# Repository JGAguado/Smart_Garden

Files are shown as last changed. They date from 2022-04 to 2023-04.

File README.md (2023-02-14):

[][documentation]
[][releases]
[](LICENSE)
[][tindie]

[][maintenance]
[][buymecoffee]

# Smart Garden
The Smart Garden is an electronic board based on the ESP32 capable of controlling a combination of 4 irrigation valves and/or water pumps, 
supporting AC & DC voltages

<p float="left">
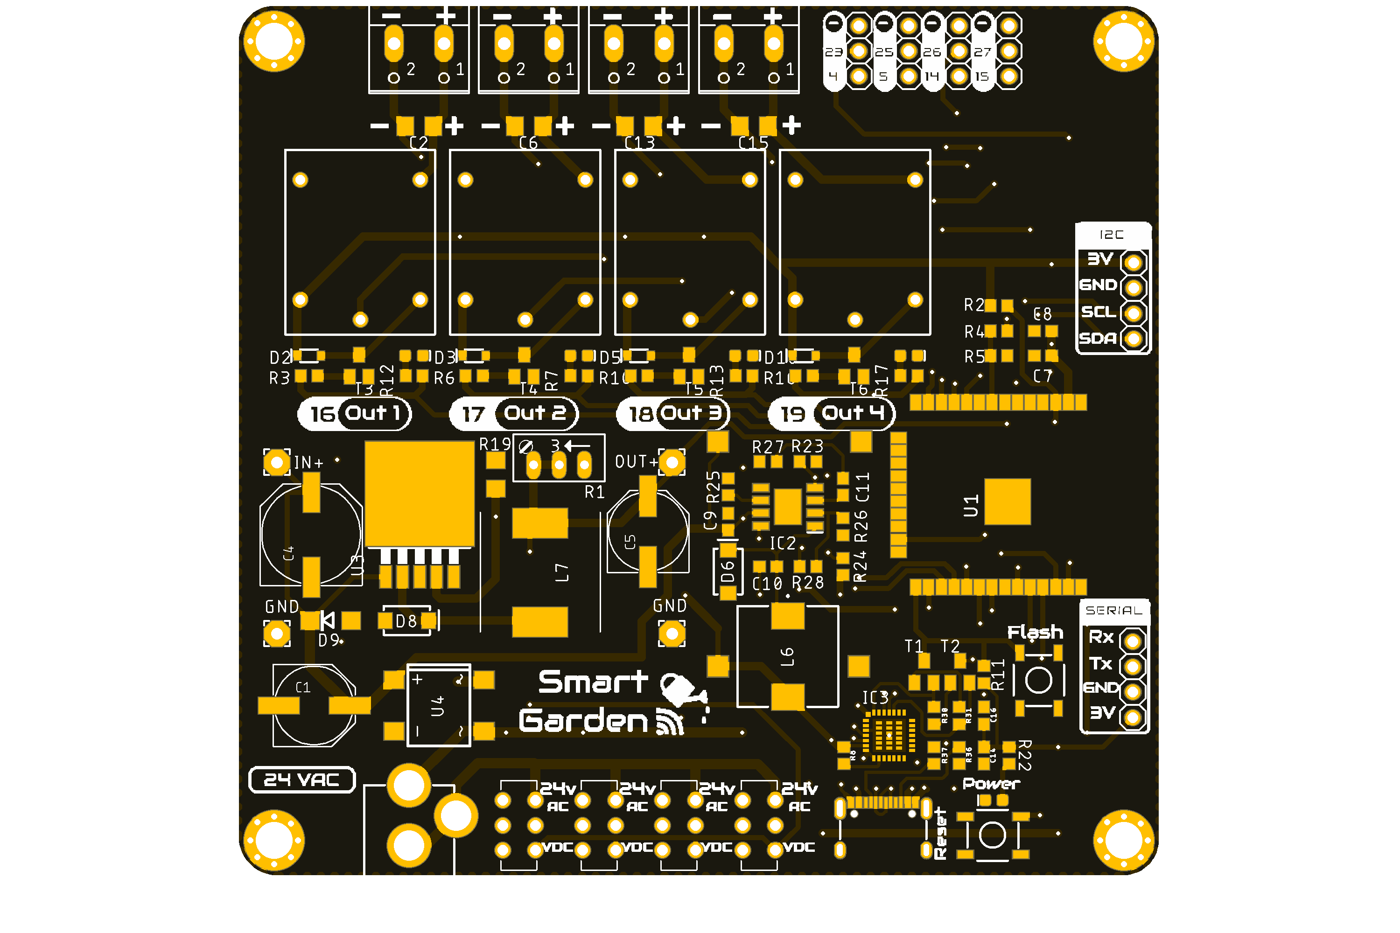
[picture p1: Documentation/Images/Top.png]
   
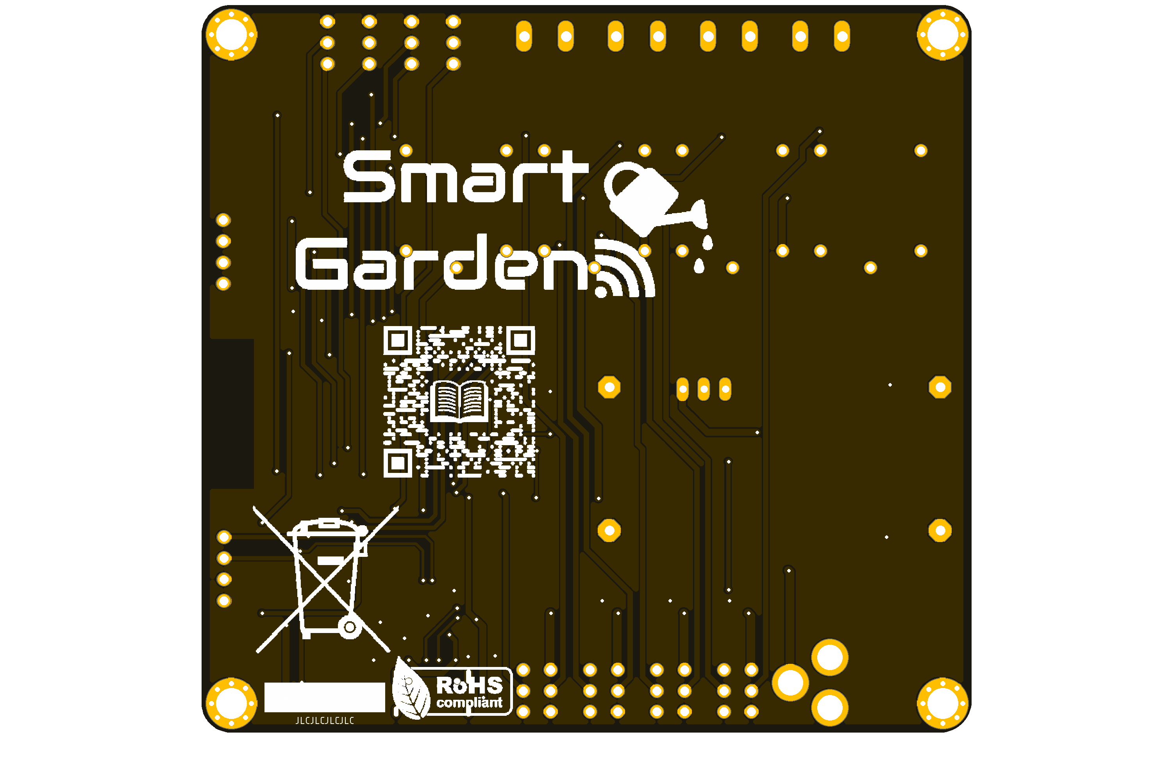
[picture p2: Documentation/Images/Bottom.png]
      
</p>

## Project tree
---
<li><a href="./Design/">Design</a></li>
<li><a href="./Documentation/">Documentation</a></li>

<li><a href="./README.md">README.md</a></li>

[documentation-shield]: https://readthedocs.org/projects/smart-garden/badge/?version=latest&style=for-the-badge
[documentation]: https://smart-garden.readthedocs.io/en/latest/

[releases-shield]: https://img.shields.io/github/release/JGAguado/Smart_Garden.svg?style=for-the-badge
[releases]: https://github.com/JGAguado/Smart_Garden/releases

[license-shield]: https://img.shields.io/badge/License-CC%20BY--NC--SA%204.0-lightgrey.svg?style=for-the-badge

[maintenance-shield]: https://img.shields.io/badge/maintainer-J.%20G.%20Aguado-blue.svg?style=for-the-badge
[maintenance]: https://github.com/JGAguado

[buymecoffee-shield]: https://img.shields.io/badge/buy%20me%20a%20coffee-support-yellow.svg?style=for-the-badge
[buymecoffee]: https://www.buymeacoffee.com/J.G.Aguado

[buyit-shield]: https://img.shields.io/badge/get%20it%20on-tindie-247d84.svg?style=for-the-badge
[tindie]: https://www.tindie.com/products/jgaguado/smart-garden/

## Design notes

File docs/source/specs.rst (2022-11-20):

Technical Specifications
========================

Electrical
----------

.. list-table:: 
    :widths: 50 20 20 20 20
    :header-rows: 1
    :stub-columns: 1

    * - Parameter
      - Symbol
      - Min.
      - Max.
      - Unit
    * - Supply voltage (AC)
      - :math:`V_{AC}`
      - 12
      - 24
      - *V*
    * - Supply voltage (DC)
      - :math:`V_{DC}`
      - 12 
      - 24
      - *V*
    * - Power
      - *P*
      -  
      - 15
      - *W*

Environment
-----------

.. list-table:: 
    :widths: 50 20 20 20 20 20
    :header-rows: 1
    :stub-columns: 1

    * - Parameter
      - Symbol
      - Min.
      - Typ.
      - Max.
      - Unit
    * - Working temperature [1]_
      - :math:`T_{amb}`
      - 0
      - 25 
      - 60
      - *°C*
    * - Storage temperature [1]_
      - :math:`T_{amb}`
      - 0
      - 25 
      - 60
      - *°C*

.. [1] Based on components datasheets.

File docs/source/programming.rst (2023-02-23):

Programming
===========

There are many firmwares supported with the |Product| (almost any supporting the ESP-32). Some of the tested working are: 
 * ESPHome
 * Tasmota
 * Arduino

In any case scenario, and regardless you are using the USB port or the Serial port for programming it, you
will first need to enter the board into flashing mode. For that, press and hold the *Flash* pushbutton
while you reset the board (pressing once the *Reset* pushbutton).

.. Caution::
    When flashing the board, make sure its only powered by the USB/Serial port.

.. Note::
    It is possible that after flashing your board and while rebooting, the ESP-32 has some issues to boot. This is due to a higher 
    demmand of power while

ESPHome
---------
`ESPHome <https://esphome.io>`_ is a well known platform for programming ESP-based devices 
with a very little effort. It is configured via YAML files and supports a wide range of functionalities
and sensors.

.. Important::
    For using ESPHome, and all its funcionalities, you need to have a `Home Assistant <https://www.home-assistant.io>`_ instance running
    in the same network as your |Product|.

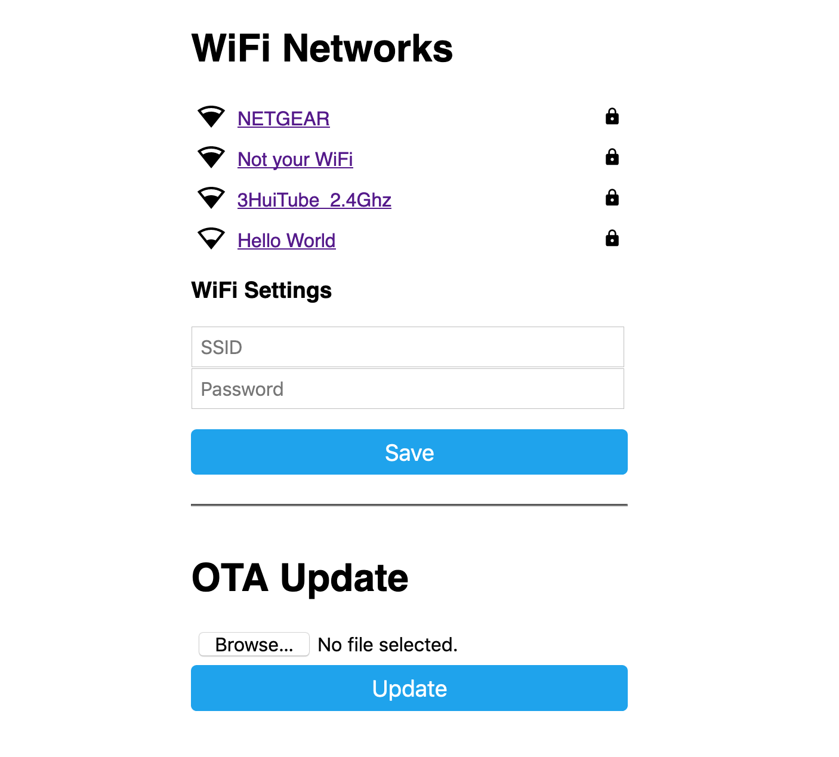
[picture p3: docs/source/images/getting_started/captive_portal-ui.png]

    
The |Product| already comes with an embeded version of ESPHome, that would only require an :term:`OTA` update
to get it ready to work in your network:

1. Power the board, and let it run for 1-2 minutes. When the board cannot connect to a WiFi network, it will 
   create a fallback hotspot.
2. Use a smartphone or tablet and go to the WiFi settings, connect to the recently created *Smart-Garden* hotspot with the password *smartgarden*.
3. Access to the captive portal and open the browser if doesn't pop up automatically.
4. Enter your network setttings and press *Save*.

Now, your ESPHome device is ready to be found by Home Assistant in your network. Add it from the ESPHome section to add 
and edit a customized configuration file.

As an example of such configuration file (and the one flashed on the factory settings of the |Product|) 
with all the :term:`I/O`:

.. literalinclude:: files/configuration.yaml
   :language: yaml
   :linenos:

Tasmota
--------
As an alternative easy-to-use and still powerfull, you can flash Tasmota into the |Product| directly. This option is higly recommendable if you want to want to have an 
Alexa compatible device (based on a Hue emulated bridge) without the need of a full Home Assistant setup.

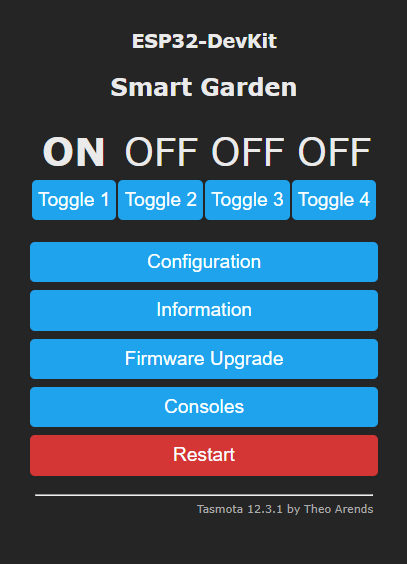
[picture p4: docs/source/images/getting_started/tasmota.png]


The easiest process of flashing Tasmota into your |Product| goes as follows:

1. Plug the |Product| into your computer's USB.
2. Go to the `Tasmota Web Installer <https://tasmota.github.io/install/>`_
3. Follow the process selecting ESP32 as device and select the correct port (remember to enter the board into flashing mode).
4. After the process is completed, press the reset button. 
5. Once rebooted, the |Product| will create a wifi hotspot containing the name *Tasmota*. Connect and enter your WLAN setup on the captive portal. 
6. Get the IP assigned to the board (check your router's connected devices) and enter it into your browser for accessing to the Tasmota's WebUI. 

Now you can customize your board as you want. Let's first assign the output class '*Relay*' to the corresponding outputs 16, 17, 18 and 19. 

In addition, some of these other commands can be entered through the **Console** (*Consoles -> Console*):

 * **Timed output**: With the command ``PulseTime3 300`` you can make that the output 3 turns off after 5 minutes (300s). This option is highly indicated as a safety feature to prevent your home to get floaded.

 * **Interlocks**: With the command ``interlock on`` you can make that ONLY one of the 4 outputs can become active at the same time. For selecting the group of the for relays just use the command ``interlock 1,2,3,4``. This mode can become usefull when your home's water pressure is not high enough for holding more than one watering zone at the same time.

In any case, you can find these and much more commands to customize your Tamota's flashed |Product| on the `official Tasmota documentation <https://tasmota.github.io/docs/Commands/>`_

.. admonition:: And, by the way...
    
    If you want Alexa to directly recognize your |Product| to directly controle each output through voice controls, go to *COnfiguration -> 
    Configure Other* and select the option 'Hue Bridge multi device' emulation.
    
Arduino
--------
If you are still interested in programming directly with the Arduino IDE, the procedure is no 
different than with any other ESP32 devices:

1. Open the Arduino IDE and go to File -> Preferences option.
2. Add to the *Additional Boards Manager URSLs* the url:

.. parsed-literal::

    https://raw.githubusercontent.com/espressif/arduino-esp32/gh-pages/package_esp32_index.json

3. Close the preferences and open in the menu Tools -> Board -> Boards Manager
4. Search for *esp32* and install it. This might take some time
5. Now you can select the board *ESP32 Dev Module* as the target board. Leave the rest of parameters 
   by default.
6. Select the correct port and remember to enter the board into flashing mode before uploading the sketch.

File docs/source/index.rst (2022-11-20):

Smart Garden
###############

.. sidebar:: |Product|

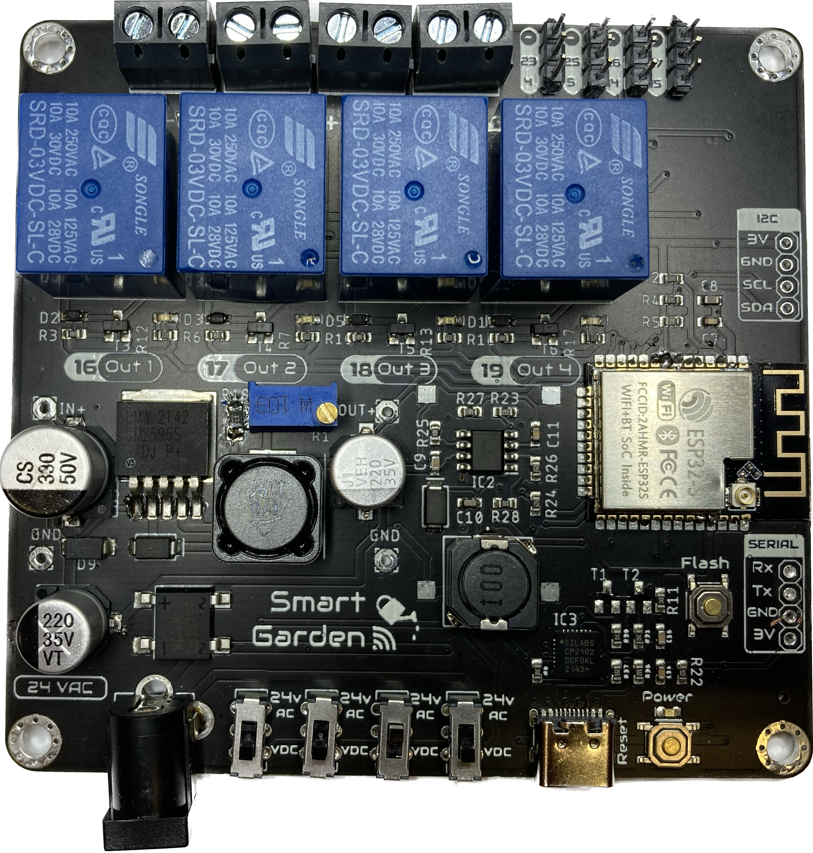
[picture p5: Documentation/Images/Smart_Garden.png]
    

Welcome to the documentation page of the |Product|, an electronic board based on the ESP32 capable of controlling a combination of 4 irrigation valves and/or water pumps, 
supporting AC & DC voltages.

Contents
--------

:doc:`safety`
    How to operate and manipulate the |Product|.

:doc:`getting_started`
    First steps for configuring and working with the |Product|.

:doc:`design`
    Design files of the |Product|.

.. _support:

Technical support
-----------------

If you have technical problems or cannot find the information that you need in the provided documentation, 
please contact me directly:

:Author: |Author|
:Contact: |Email|

:Board: |Product|
:Revision: |Release|
:Date: |Date|

.. toctree::
   :caption: Safety Guidelines
   :maxdepth: 2
   :hidden:

   safety
   
.. toctree::
   :caption: First steps
   :maxdepth: 2
   :hidden:

   getting_started
   programming
   faq

.. toctree::  
   :caption: Design
   :maxdepth: 2
   :hidden:
   
   design   
   specs

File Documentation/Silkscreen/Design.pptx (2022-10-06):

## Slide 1

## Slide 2

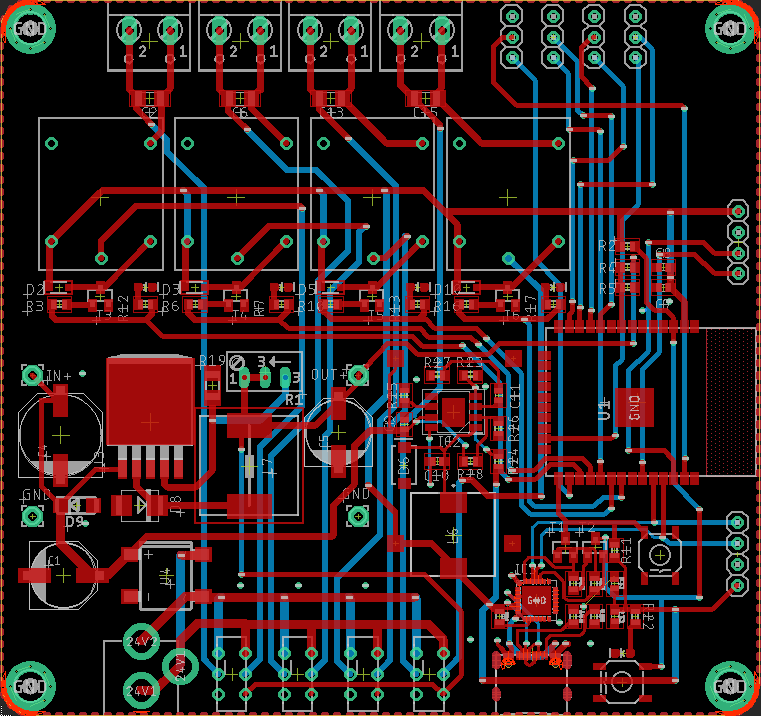
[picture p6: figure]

Out 1

16

Out 2

17

Out 3

18

Out 4

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
Flash

SERIAL

3V

GND

Tx

Rx

Smart Garden

24VAC

24VAC

24VAC

24VAC

24 VAC

Power

VDC

VDC

VDC

VDC

Reset

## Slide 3

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
Out 1

16

Out 2

17

Out 3

18

Out 4

19

Flash

SERIAL

3V

GND

Tx

Rx

Smart Garden

24VAC

24VAC

24VAC

24VAC

24 VAC

Power

VDC

VDC

VDC

VDC

Reset

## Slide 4

Smart Garden

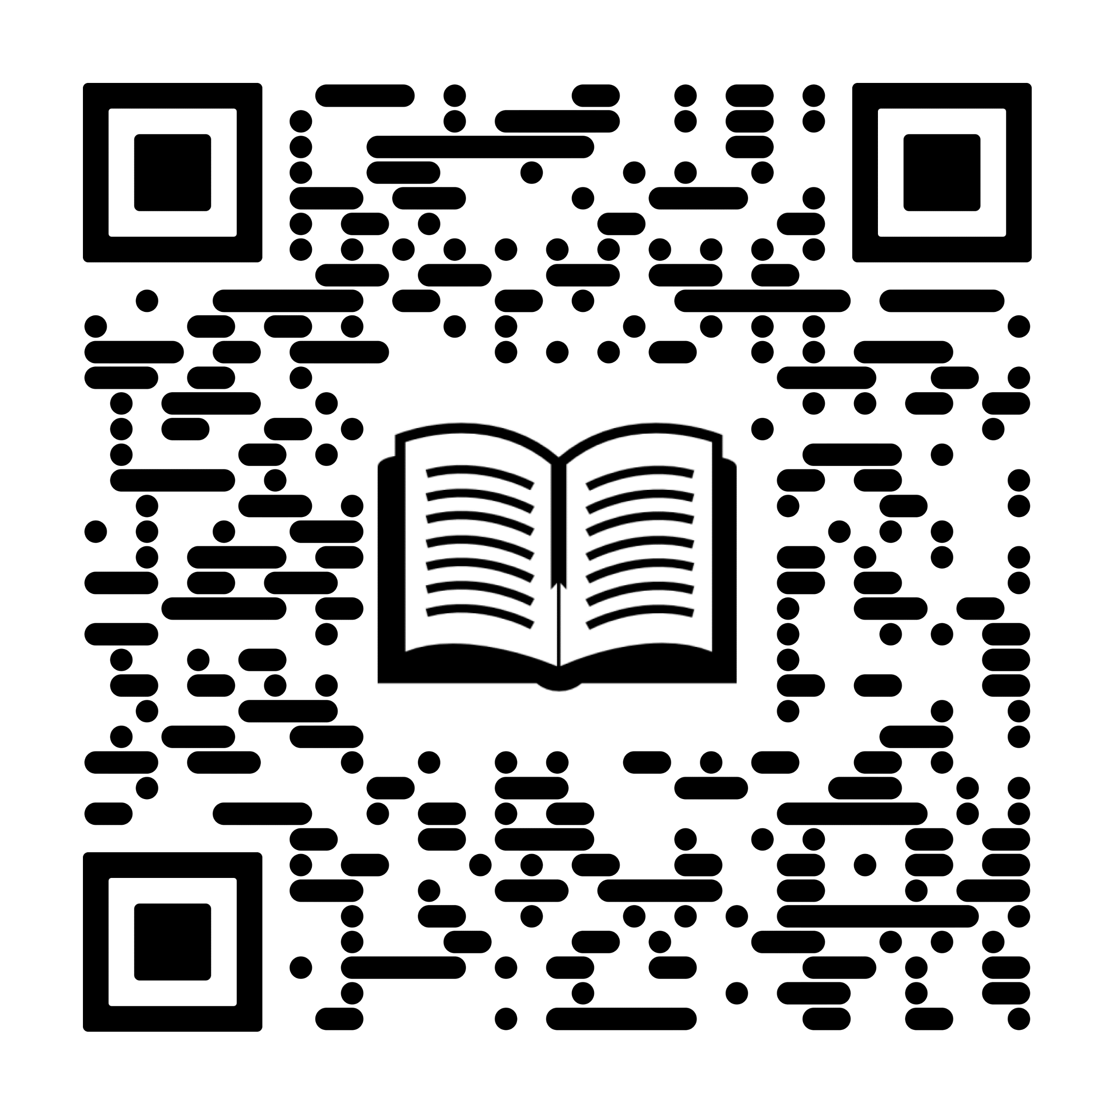
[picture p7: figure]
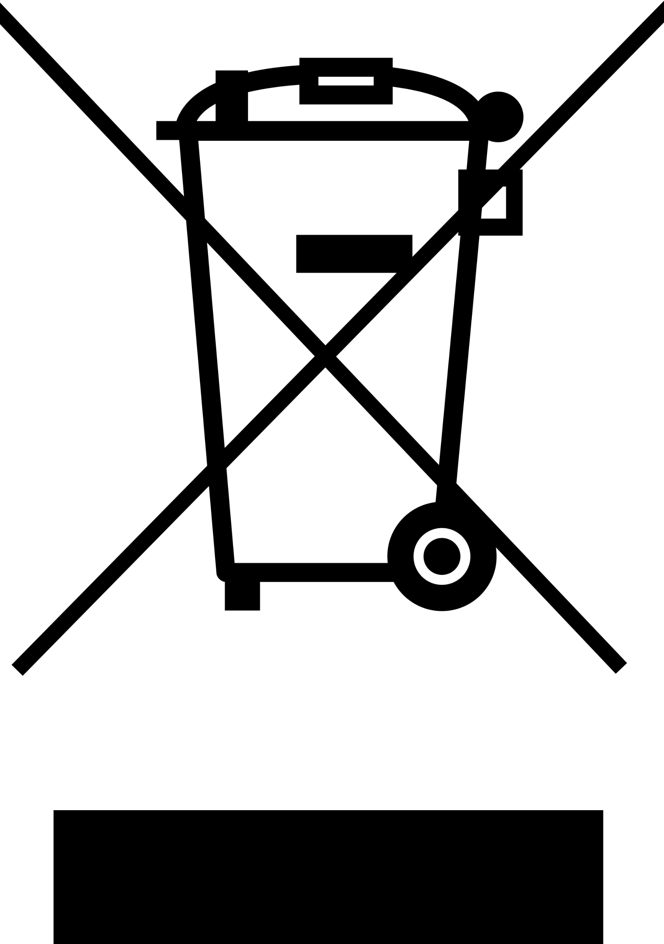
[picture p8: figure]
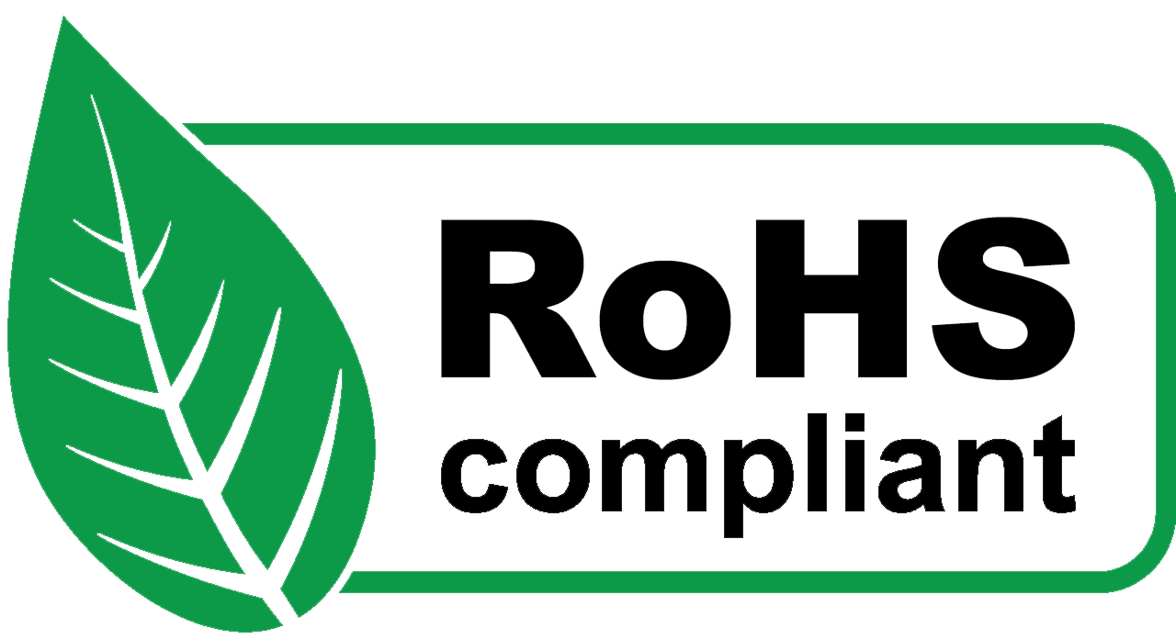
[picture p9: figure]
Umweltrichtlinien

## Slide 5

Smart Garden

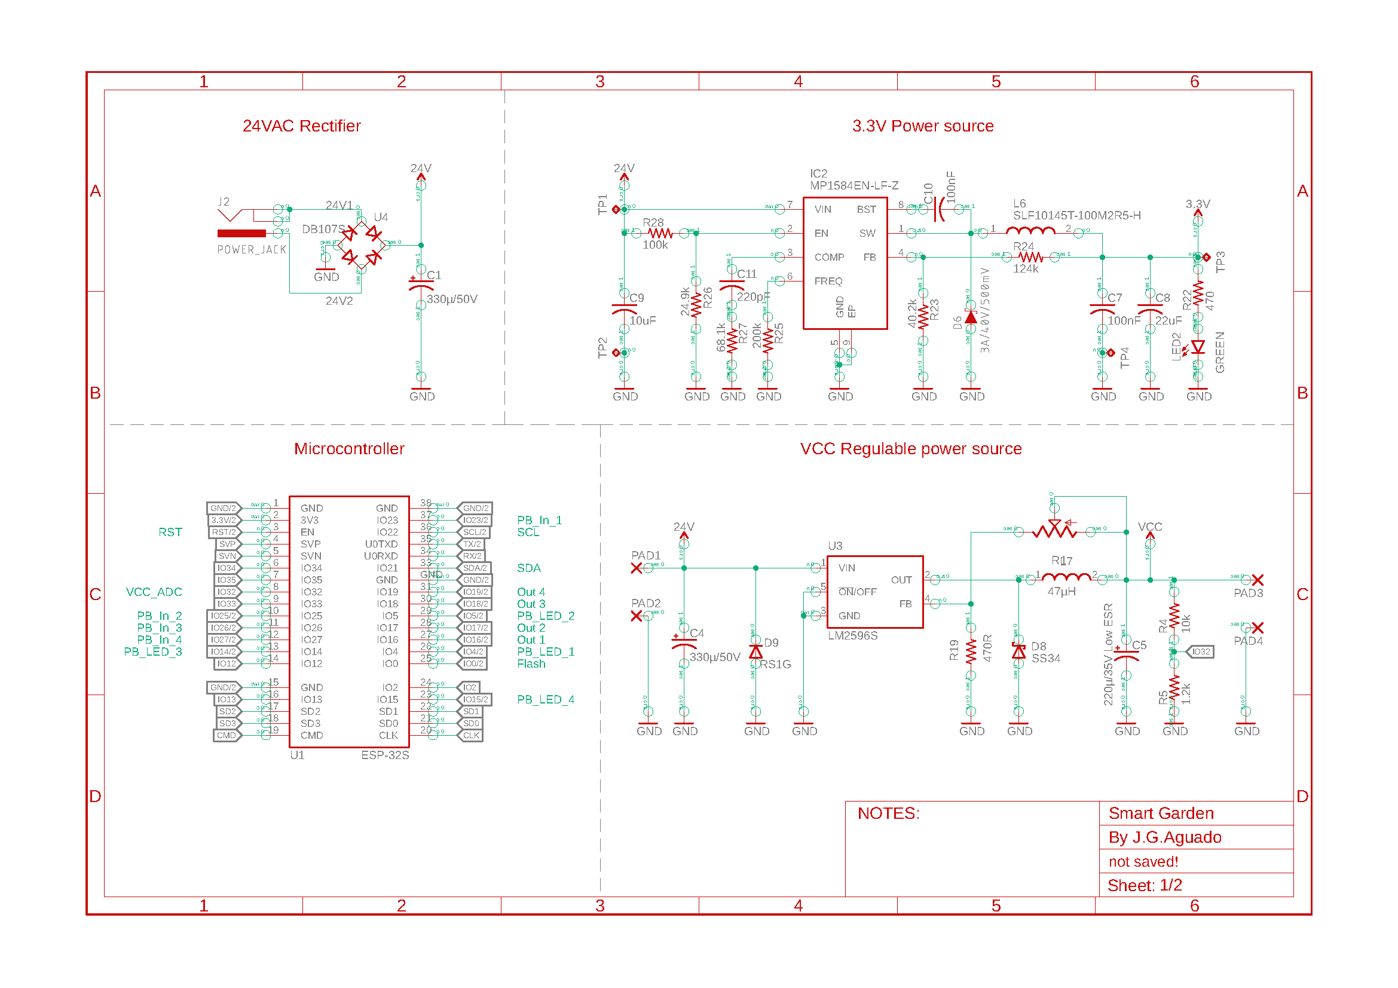
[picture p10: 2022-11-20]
Documentation/Schematics/Schematic_1.png

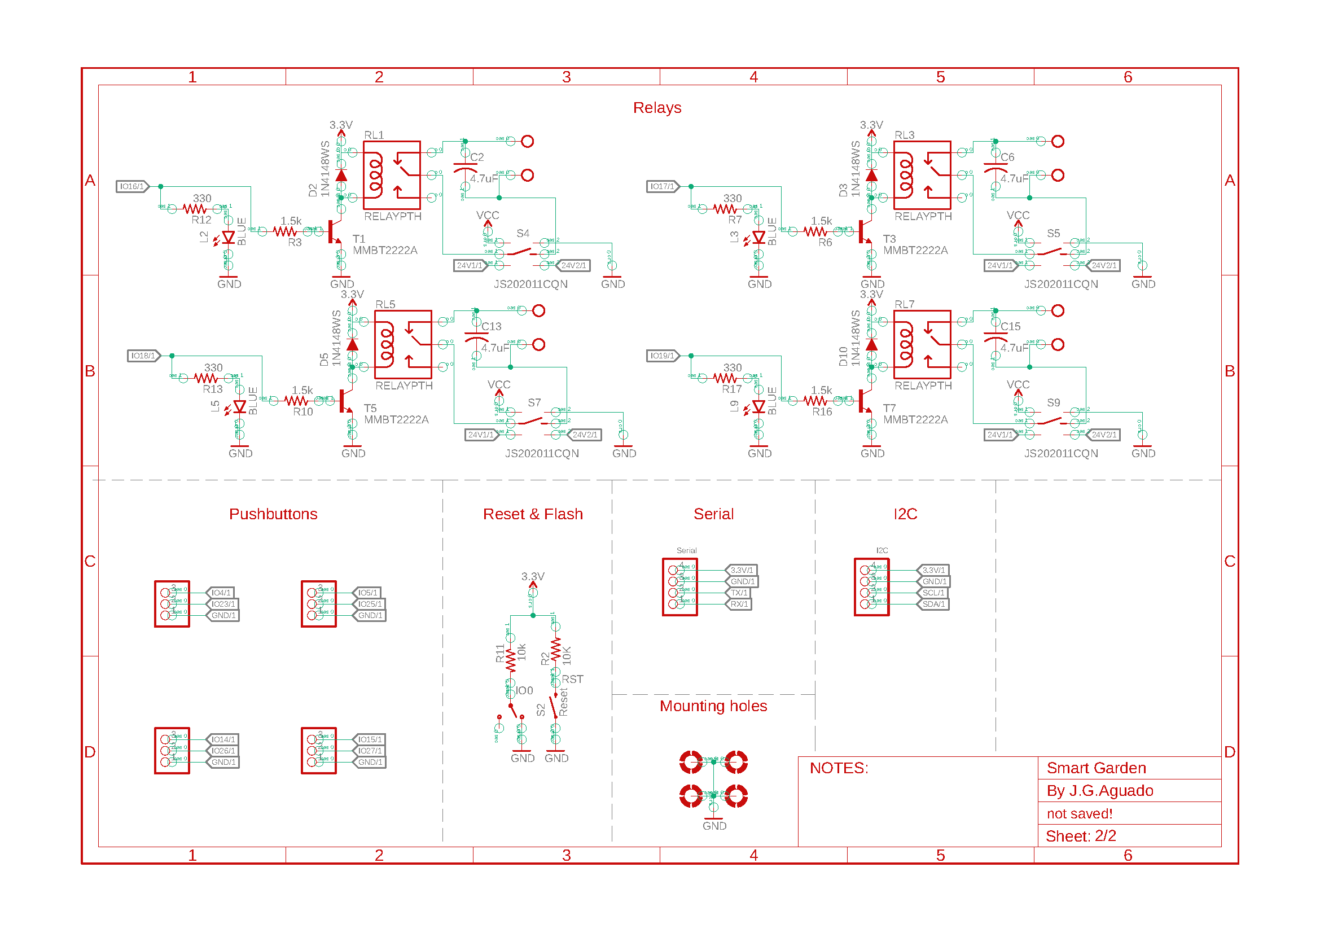
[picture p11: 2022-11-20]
Documentation/Schematics/Schematic_2.png

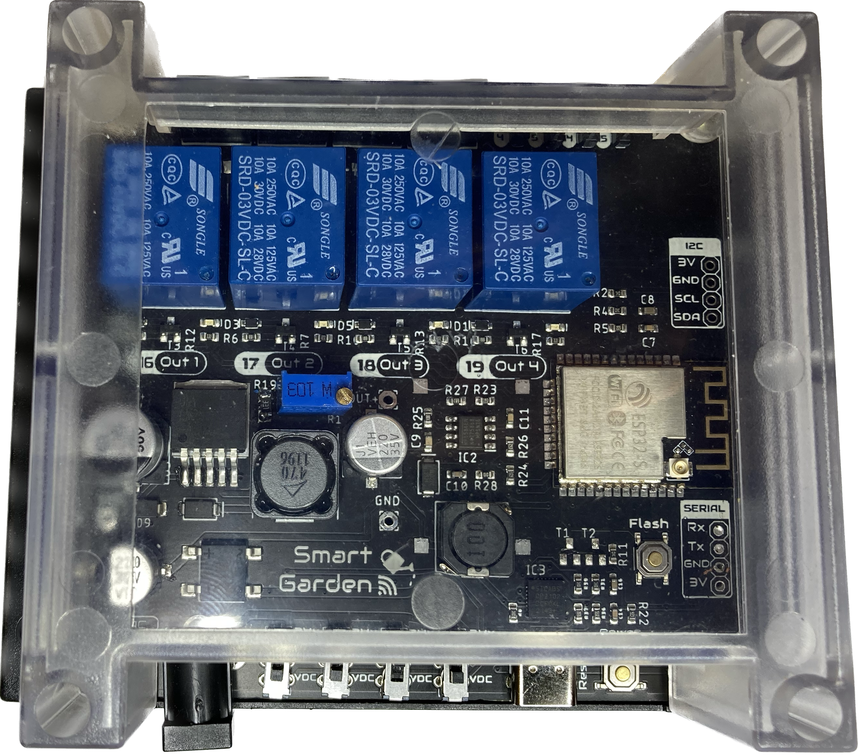
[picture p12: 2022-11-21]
Documentation/Images/SG_Enclosed_Top.png

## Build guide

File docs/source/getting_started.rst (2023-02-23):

Getting started
===============

Soldering 
----------
.. Important::
    Please note that some components in this board need to be soldered.

If you have never soldered or you want to improve your soldering techniques I recommend you 
the `Adafruit Guide To Excellent Soldering <https://learn.adafruit.com/adafruit-guide-excellent-soldering>`_

For better understanding where is located each component on the board check out the :ref:`pcb` layout 
with the interactive :term:`BOM`.

Powering
--------
.. Caution::
    Power the board only after making all the connections

The |Product| is powered directly through a Power Jack connector located on the bottom part of the board. The recommended 
size for the input connector is a 5.5mm (outer) and 2.1mm (inner) diameter power jack.

As the |Product| was designed to control sprinkles, it is expected to be powered with a 24VAC source, such as the **NIMO YL15-2401000 220VAC to 24VAC (1A)**. 

Alternatively, and if you are not expecting to control AC sprinkles, powering the board from any VDC in the range of 12-24V is posible as well.

.. Note::
    Choose always a power supply that can deliver the same or more (within the :doc:`specs` limits) voltage than your loads (solenoid valves/ pumps), as the DC/DC 
    regulator operates as a step-down converter.

I/O
-----------
The |Product| supports up to 4 independent *analog outputs*  and 8 *digital inputs/outputs*:

.. _pinout:

.. list-table:: Pinout table
    :widths: 10 10 10 20
    :header-rows: 1

    * - GPIO
      - Input
      - Output
      - Name
    * - 4
      - ✅
      - ✅
      - Auxiliar 1A
    * - 5
      - ✅
      - ✅
      - Auxiliar 2A
    * - 14
      - ✅
      - ✅
      - Auxiliar 3A
    * - 15
      - ✅
      - ✅
      - Auxiliar 4A
    * - 16
      - ❌
      - ✅
      - Output 1
    * - 17
      - ❌
      - ✅
      - Output 2
    * - 18
      - ❌
      - ✅
      - Output 3
    * - 19
      - ❌
      - ✅
      - Output 4
    * - 23
      - ✅
      - ✅
      - Auxiliar 1B
    * - 25
      - ✅
      - ✅
      - Auxiliar 2B
    * - 26
      - ✅
      - ✅
      - Auxiliar 3B
    * - 27
      - ✅
      - ✅
      - Auxiliar 4B

Outputs:
^^^^^^^^^^^^^^^^
Each one of these outputs are individually controlled through relays, so the can only be on True/False states. However, the type of output voltage can be 
assigned previously via hardware: 

Next to the power jack connector, there are 4 slide switches that configure each of the 4 outputs as DC or AC:

* If the *24 VAC* is selected, the controlled relay will output 0 or 24VAC. This is the way to control solenoid valves such as the `Hunter PGV series <https://www.hunterindustries.com/en-metric/node/28321>`_ 
  or the `Gardena's Irrigation Valve 24V <https://www.gardena.com/int/products/watering/water-controls/24-v-irrigation-valve/900904101/>`_ 

* If the *VDC* is selected, the controlled relay will output 0 or a regulated VDC voltage. This DC voltage can be adjusted through the blue trimmer in a range of 3.3 up to the input
  voltage through the jack connector. This is the way to control DC water pumps up to 10W. 

The connection port of each of the outputs is located on the top left part of the board and is done through 
3.5mm screw terminals. The polarity of the connection (for DC operations) is defined on the PCB silkscreen.



From left to right, the pin definion of each output is:

:Output 1: *GPIO16*
:Output 2: *GPIO17*
:Output 3: *GPIO18*
:Output 4: *GPIO19*

Digital inputs/outputs:
^^^^^^^^^^^^^^^^^^^^^^^
The connection port of these pins is located on the top right part of the board and is done through 
2.54 pins.



These pins are grouped in 4 sets, containing: 
:Auxiliar 1: *GND*, *GPIO23* & *GPIO4*
:Auxiliar 2: *GND*, *GPIO25* & *GPIO5*
:Auxiliar 3: *GND*, *GPIO26* & *GPIO14*
:Auxiliar 4: *GND*, *GPIO27* & *GPIO15*

.. Hint::
    These pins can be used to read if ring led powered pushbuttons has been pressed.

Analog inputs:
^^^^^^^^^^^^^^
In order to provide a feedback of the DC regulated voltage that would be output, pin *GPIO32* offers a measurement of the real voltage once regulated.

Since it is designed in a voltage divider configuration for avoiding the input read above 3.3V to the microcontroller, the correspondent equation for obtaining 
the real voltage is as follows:

:math:`V_{real} = \frac{11.2k\Omega}{1.2k\Omega} \cdot V_{measured} = 9.33 \cdot V_{measured}`

Communications
-----------
In addition to the I/O mentioned before, there is also a direct connection to:

:term:`IIC` (:math:`I^2C`) bus:
^^^^^^^^
:SDA: *GPIO21*
:SCL: *GPIO22*

Serial bus:
^^^^^^^^^^^
:Tx: *GPIO1*
:Rx: *GPIO3*

Enclosure
---------
The |Product| has been designed to fit in the electronics enclosure LK-PLC01,
compatible with DIN rails and screws, and it is recommended for indoors only.

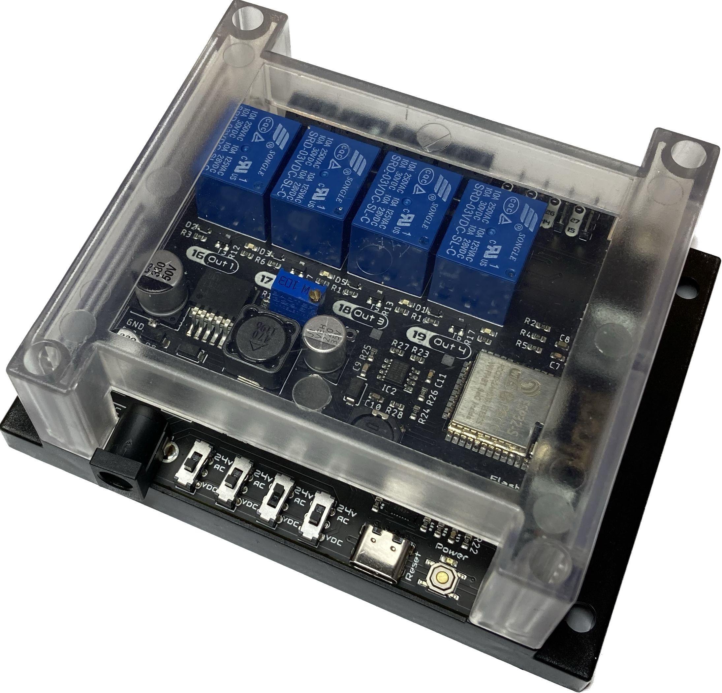
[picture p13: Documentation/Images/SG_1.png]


:External size: 115x90x40mm
:Material: ABS Plastic
:Color: Transparent cover, black or beige base

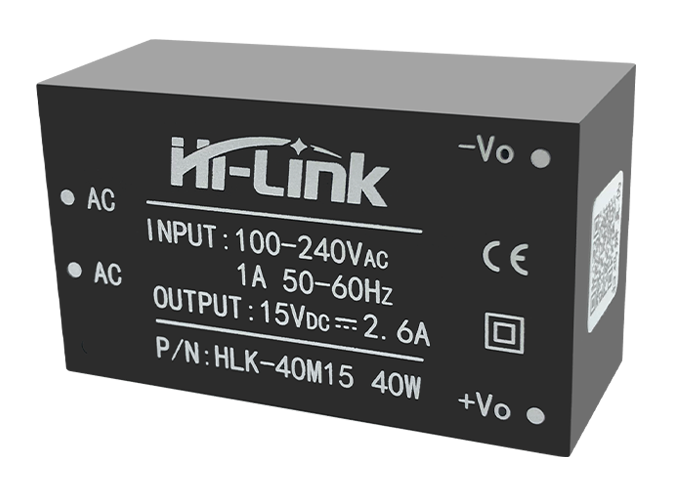
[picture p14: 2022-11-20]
docs/source/images/assembly/HLK-40.png

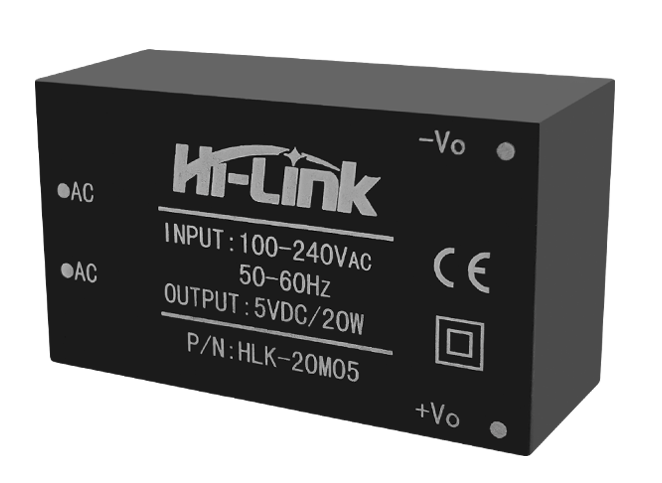
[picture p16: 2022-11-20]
docs/source/images/assembly/HLK-20.png

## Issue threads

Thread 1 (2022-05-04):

Flash arrow

JGAguado, 2022-05-04:
Fix the direction of the flash arrow silkscreen

Closed 2022-11-12.

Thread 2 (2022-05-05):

Jack connector

JGAguado, 2022-05-05:
Fix polarity connector

Closed 2022-11-12.

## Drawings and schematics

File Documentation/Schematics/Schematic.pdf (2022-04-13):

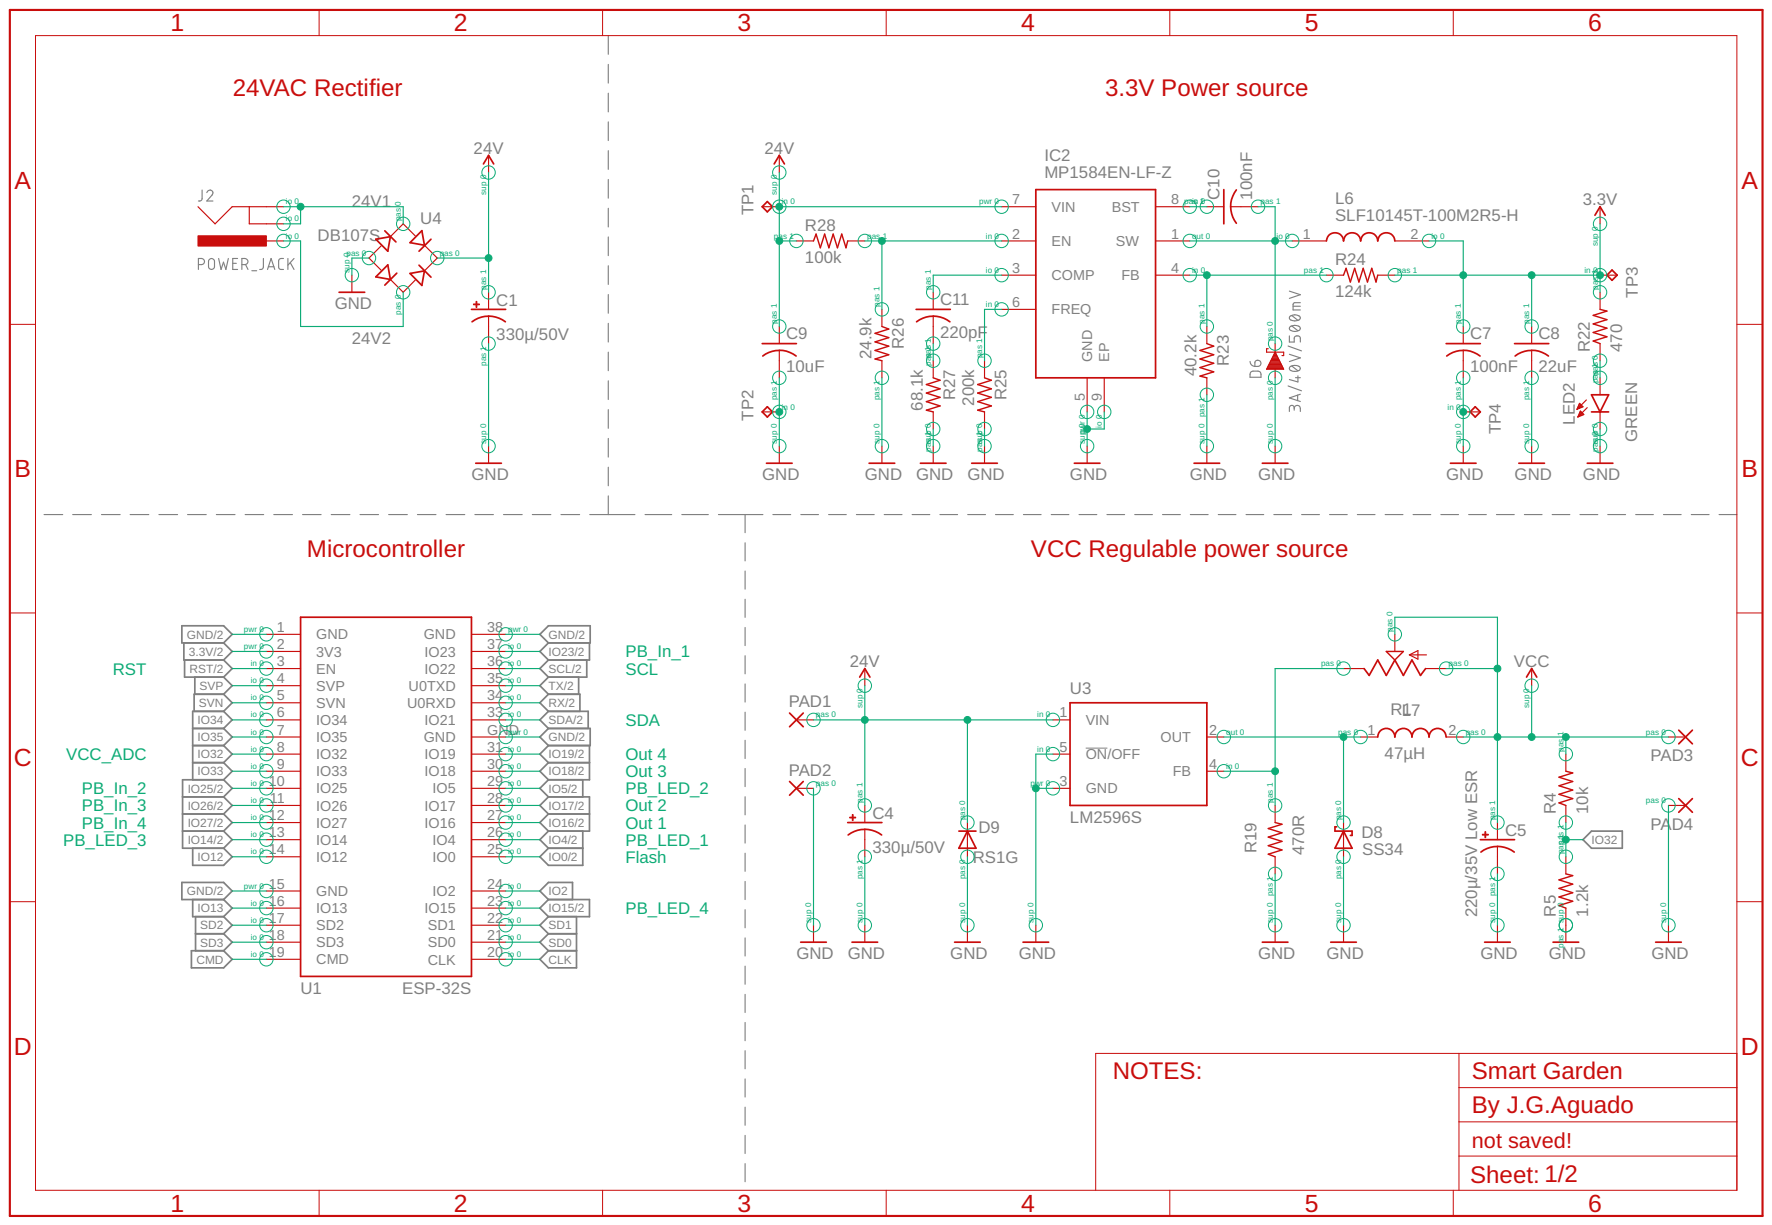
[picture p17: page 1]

pas 1 pas 1 pas 0 pas 0 sup 0 sup 0

pas 1 pas 1

pas 1 pas 1 pas 1 pas 1 sup 0

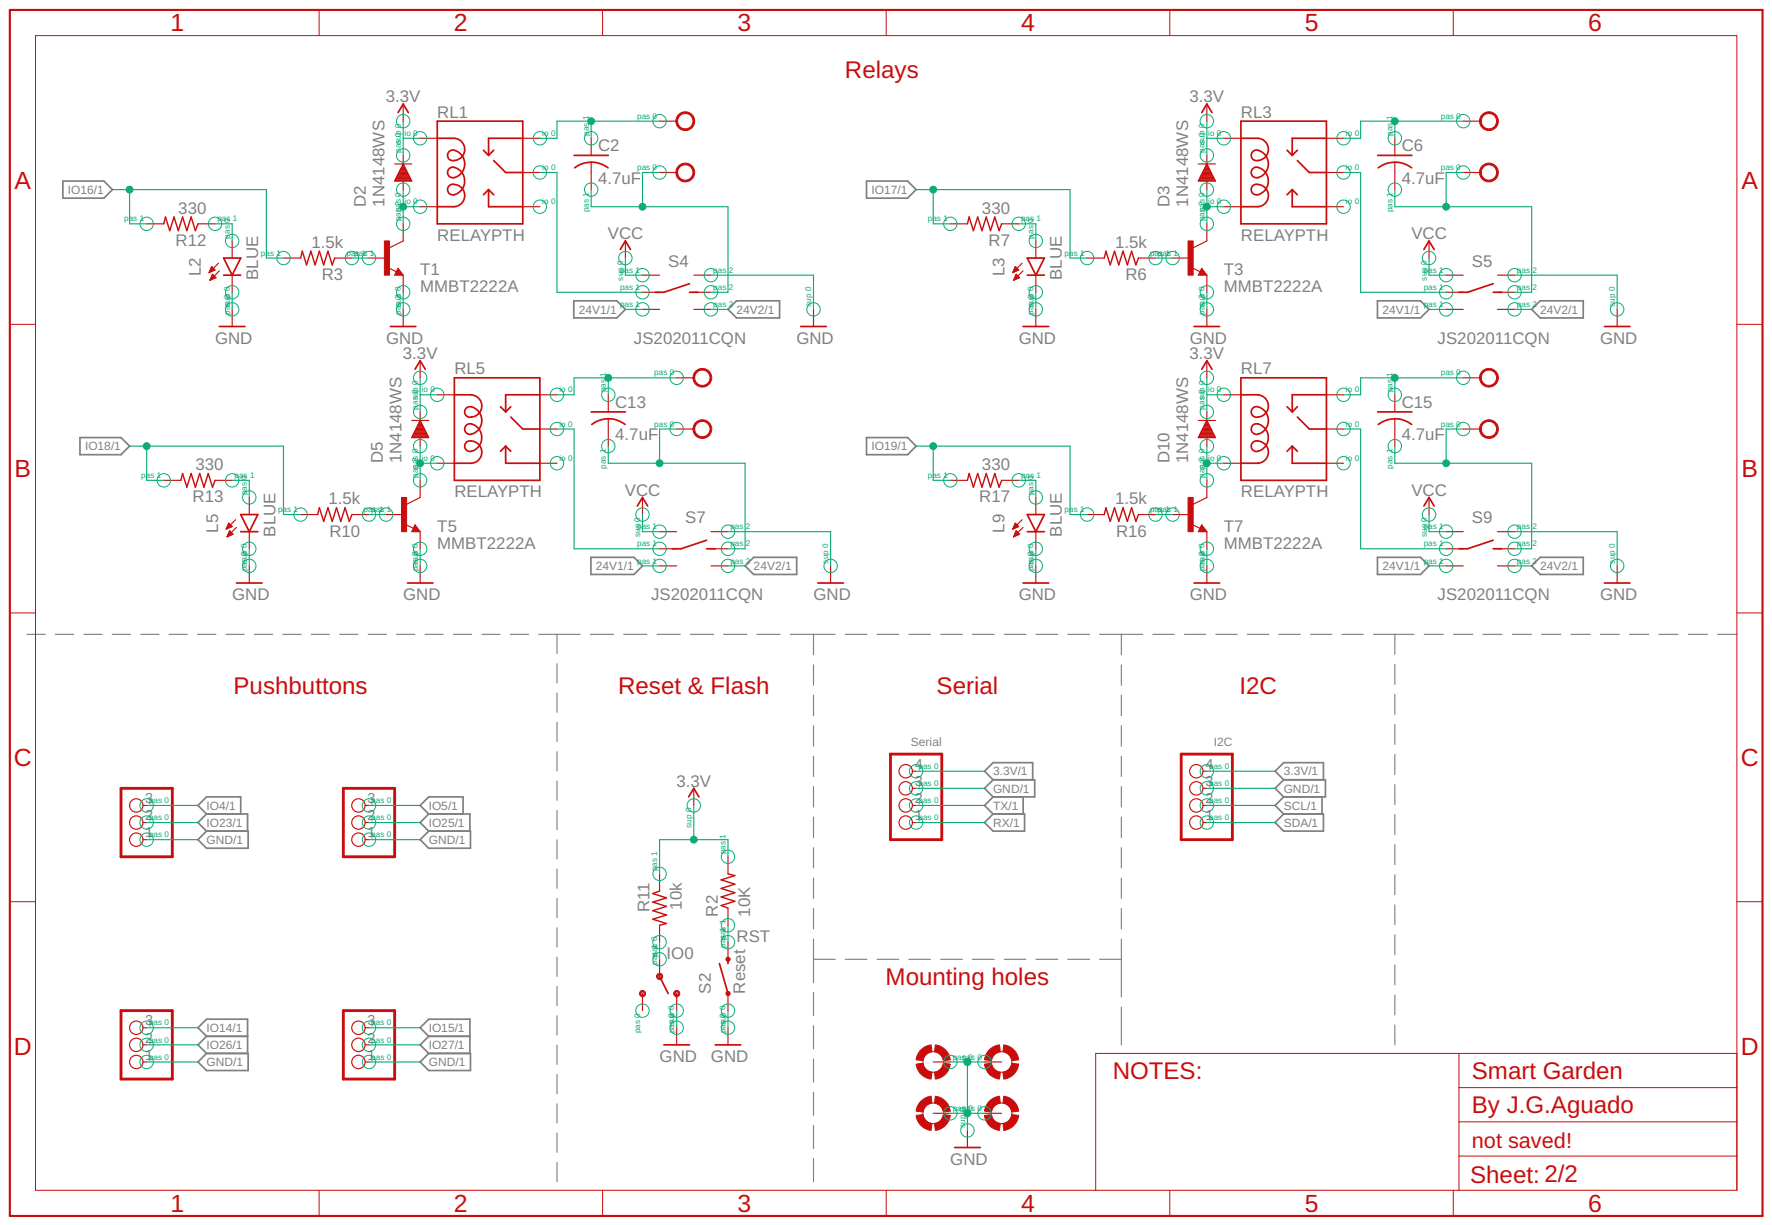
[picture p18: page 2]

pas 3 pas 2 pas 0 pas 0

SCL/1 SDA/1 Mounting holes

pas 1 pas 1 sup 0 pas 2 pas 1

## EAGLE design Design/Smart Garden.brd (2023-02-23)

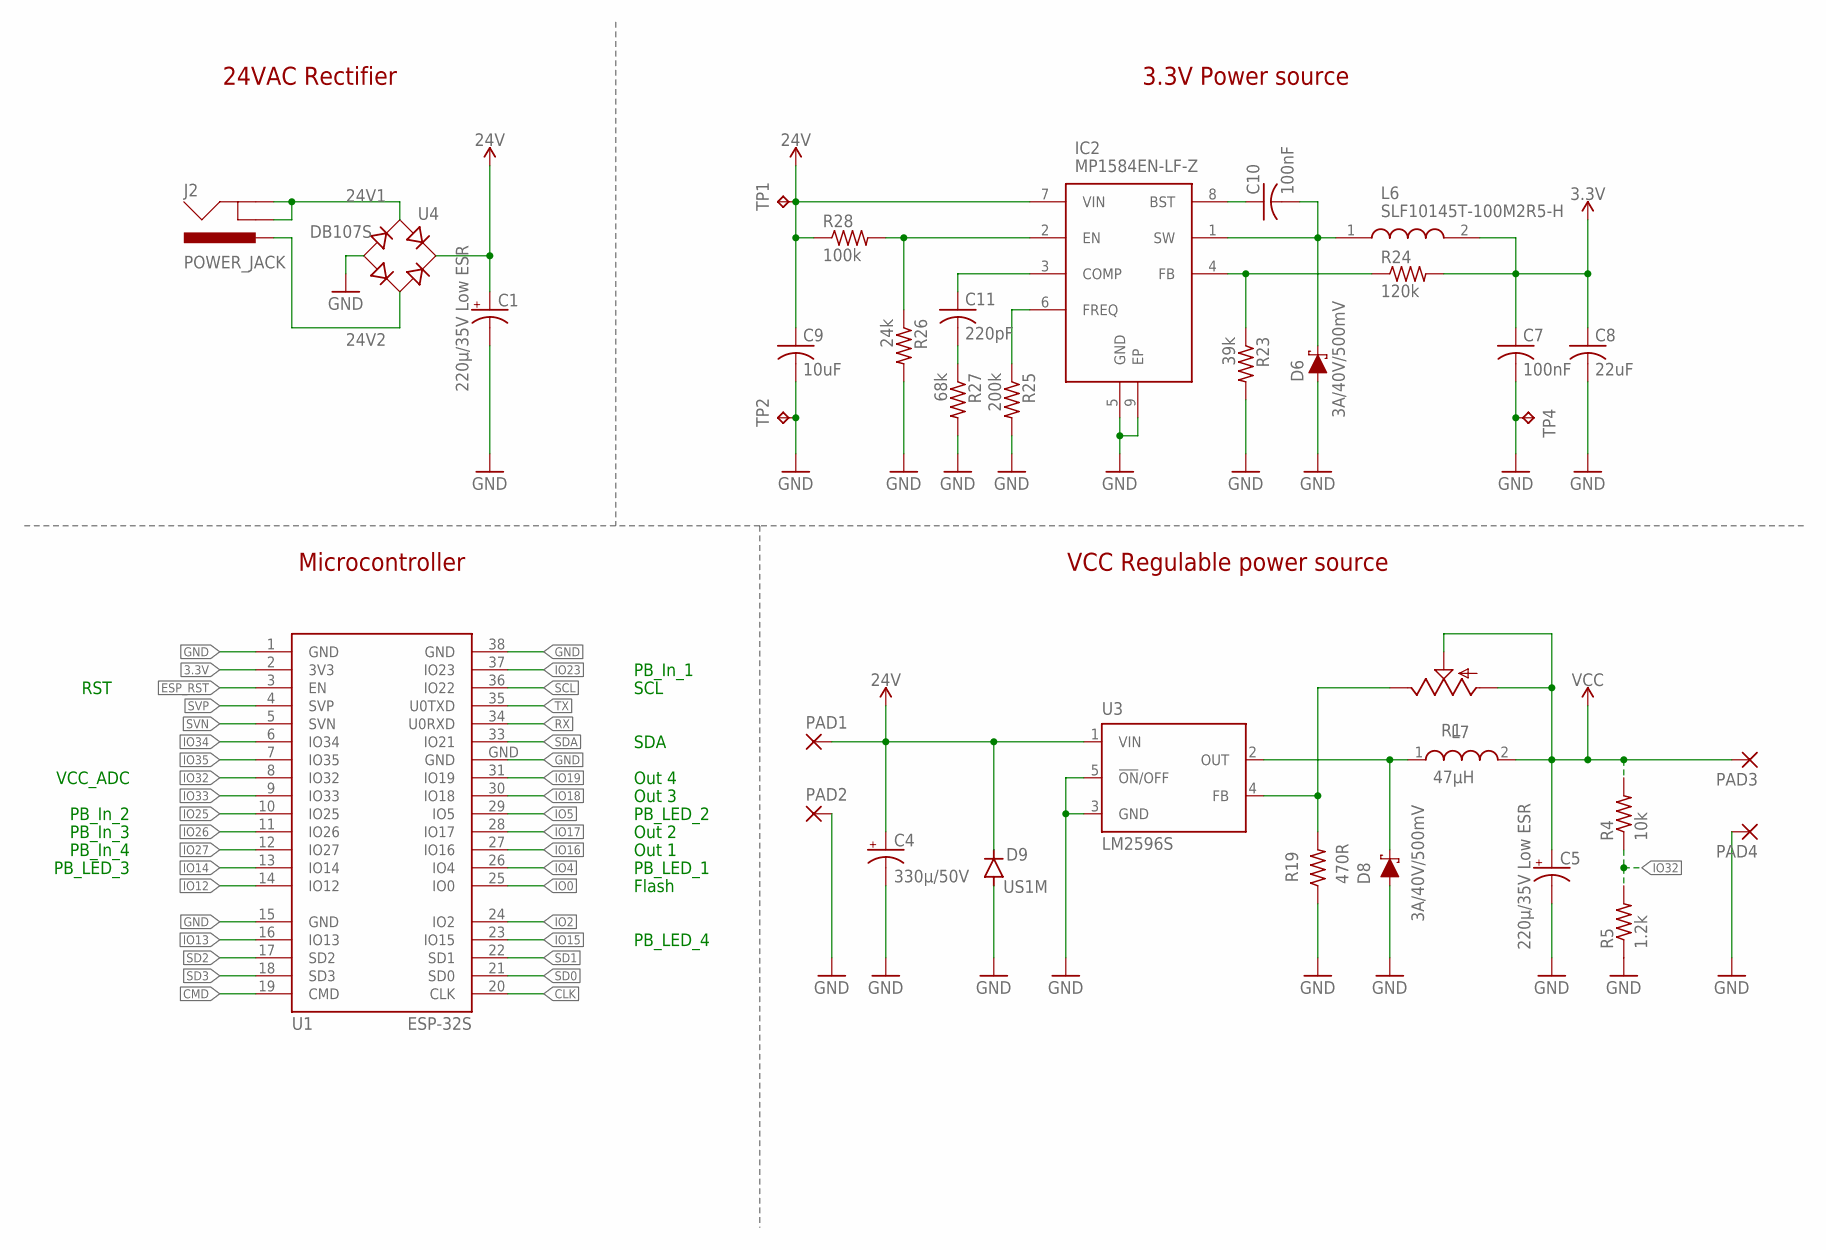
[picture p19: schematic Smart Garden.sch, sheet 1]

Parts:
C1, C5: 220µ/35V Low ESR; PANASONIC_F
C4: 330µ/50V; PANASONIC_G
C7, C10: 100nF; C0603
C8: 22uF; C0603
C9: 10uF; C0603
C11: 220pF; C0603
D6, D8: 3A/40V/500mV; SMA-DIODE
D9: US1M; DO214AC
IC2: MP1584EN-LF-Z; SOIC127P600X170-9N
J2: POWER_JACK; POWER_JACK_PTH
L6: SLF10145T-100M2R5-H; SLF10145
L7: 47µH; WE-PD_1260/1245/1280/1210
PAD1, PAD2, PAD3, PAD4: 2,54/1,1
R1: TRIM_US-RJ9W; RJ9W
R4: 10k; R0603; LCSC C25804
R5: 1.2k; R0603
R19: 470R; R1206
R23: 39k; R0603
R24: 120k; R0603
R25: 200k; R0603
R26: 24k; R0603
R27: 68k; R0603
R28: 100k; R0603
TP1, TP2, TP4: TPTP20SQ; TP20SQ
U1: ESP-32S
U3: LM2596S; TO263-5
U4: DB107S; DBS; LCSC C5377

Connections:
3.3V: C7.1, C8.1, L6.2, R24.2, U1.2 (3V3); also elsewhere on the board
24V: C1.+, C4.+, C9.1, D9.C, IC2.7 (VIN), PAD1.1, R28.1, TP1.TP, U3.1 (VIN), U4.+
24V1: J2.GND, J2.GNDBREAK, U4.AC1; also elsewhere on the board
24V2: J2.PWR, U4.AC2; also elsewhere on the board
CLK: U1.20 (CLK)
CMD: U1.19 (CMD)
ESP_RST: U1.3 (EN); also elsewhere on the board
GND: C1.-, C4.-, C5.-, C7.2, C8.2, C9.2, D6.A, D8.A, D9.A, IC2.5 (GND), IC2.9 (EP), PAD2.1, PAD4.1, R5.1, R19.1, R23.2, R25.2, R26.2, R27.2, TP2.TP, TP4.TP, U1.1 (GND), U1.15 (GND), U1.38 (GND), U1.GND, U3.3 (GND), U3.5 (!ON!/OFF), U4.-; also elsewhere on the board
IO0: U1.25 (IO0); also elsewhere on the board
IO2: U1.24 (IO2)
IO4: U1.26 (IO4); also elsewhere on the board
IO5: U1.29 (IO5); also elsewhere on the board
IO12: U1.14 (IO12)
IO13: U1.16 (IO13)
IO14: U1.13 (IO14); also elsewhere on the board
IO15: U1.23 (IO15); also elsewhere on the board
IO16: U1.27 (IO16); also elsewhere on the board
IO17: U1.28 (IO17); also elsewhere on the board
IO18: U1.30 (IO18); also elsewhere on the board
IO19: U1.31 (IO19); also elsewhere on the board
IO23: U1.37 (IO23); also elsewhere on the board
IO25: U1.10 (IO25); also elsewhere on the board
IO26: U1.11 (IO26); also elsewhere on the board
IO27: U1.12 (IO27); also elsewhere on the board
IO32: R4.1, R5.2, U1.8 (IO32)
IO33: U1.9 (IO33)
IO34: U1.6 (IO34)
IO35: U1.7 (IO35)
unnamed: D8.C, L7.1, U3.2 (OUT)
unnamed: R1.E, R19.2, U3.4 (FB)
unnamed: C10.1, IC2.8 (BST)
unnamed: C10.2, D6.C, IC2.1 (SW), L6.1
unnamed: IC2.4 (FB), R23.1, R24.1
unnamed: C11.2, R27.1
unnamed: C11.1, IC2.3 (COMP)
unnamed: IC2.6 (FREQ), R25.1
unnamed: IC2.2 (EN), R26.1, R28.2
RX: U1.34 (U0RXD); also elsewhere on the board
SCL: U1.36 (IO22); also elsewhere on the board
SD0: U1.21 (SD0)
SD1: U1.22 (SD1)
SD2: U1.17 (SD2)
SD3: U1.18 (SD3)
SDA: U1.33 (IO21); also elsewhere on the board
SVN: U1.5 (SVN)
SVP: U1.4 (SVP)
TX: U1.35 (U0TXD); also elsewhere on the board
VCC: C5.+, L7.2, PAD3.1, R1.A, R1.S, R4.2; also elsewhere on the board

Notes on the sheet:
Out 1
Out 2
Out 3
Out 4
Flash
SDA
SCL
PB_In_1
PB_LED_1
PB_In_2
PB_In_3
PB_In_4
PB_LED_4
PB_LED_3
PB_LED_2
RST
VCC_ADC
24VAC Rectifier
3.3V Power source
VCC Regulable power source
Microcontroller

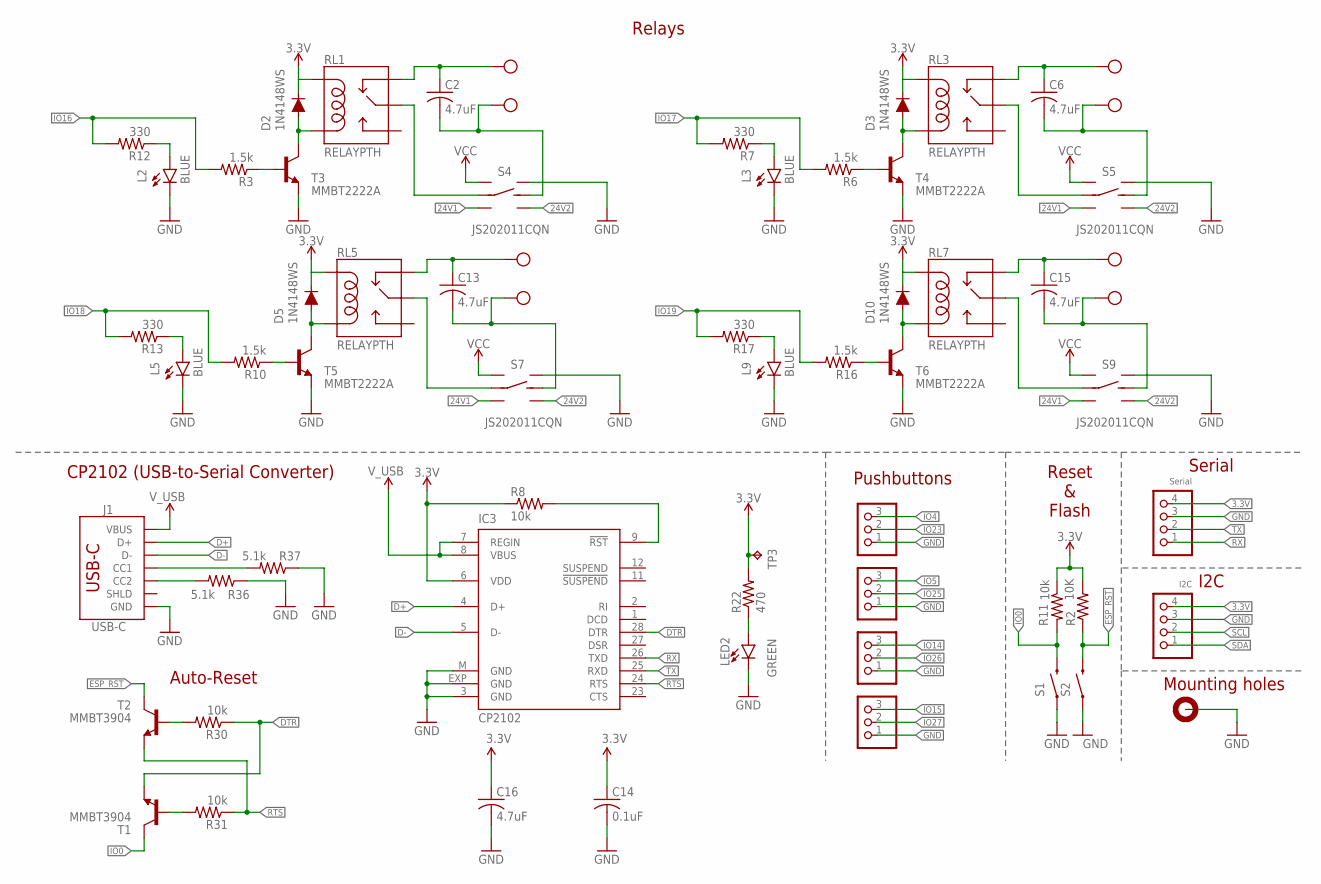
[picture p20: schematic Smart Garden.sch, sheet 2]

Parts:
C2, C6, C13, C15: 4.7uF; C1206; LCSC C29823
C14: 0.1uF; C0603
C16: 4.7uF; C0603
D2, D3, D5, D10: 1N4148WS; SOD-323
H1: 92X84; 92X87
IC3: CP2102; MLP28
J1: USB-C; USB-C-16P-4LAYER-ISOLATED
JP1: Serial; 1X04
JP2, JP3, JP4, JP5: PINHD-1X3; 1X03
JP6: I2C; 1X04
L2, L3, L5, L9: BLUE; LED-0603
LED2: GREEN; LED-0603; LCSC C72043
R2: 10K; R0603; LCSC C25804
R3, R6, R10, R16: 1.5k; R0603; LCSC C22843
R7, R12, R13, R17: 330; R0603
R8, R30, R31: 10k; R0603
R11: 10k; R0603; LCSC C25804
R22: 470; R0603
R36, R37: 5.1k; R0603
RL1, RL3, RL5, RL7: RELAYPTH; SRD-05VDC-SL-C
S1, S2: Reset; TACTILE_SWITCH_SMD_5.2MM
S4, S5, S7, S9: JS202011CQN; DPDT_JS202011CQN
T1, T2: MMBT3904; SOT23-BEC
T3, T4, T5, T6: MMBT2222A; SOT23; LCSC C8512
TP3: TPTP20SQ; TP20SQ
X2, X4, X6, X7: W237-102

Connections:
3.3V: C14.1, C16.1, D2.C, D3.C, D5.C, D10.C, IC3.6 (VDD), JP1.4, JP6.4, R2.2, R8.1, R11.1, R22.2, RL1.COIL1, RL3.COIL1, RL5.COIL1, RL7.COIL1, TP3.TP; also elsewhere on the board
24V1: S4.3 (L2), S5.3 (L2), S7.3 (L2), S9.3 (L2); also elsewhere on the board
24V2: S4.6 (R2), S5.6 (R2), S7.6 (R2), S9.6 (R2); also elsewhere on the board
CC3: J1.B5 (CC2), R36.2
CC4: J1.A5 (CC1), R37.2
D+: IC3.4 (D+), J1.A6 (D+), J1.B6 (D+)
D-: IC3.5 (D-), J1.A7 (D-), J1.B7 (D-)
DTR: IC3.28 (DTR), R30.1, T1.E
ESP_RST: R2.1, S2.3 (2), T2.C; also elsewhere on the board
GND: C14.2, C16.2, H1.B3,1, H1.B3,2, H1.B3,3, H1.B3,6, H1.P$1, H1.P$2, H1.P$3, H1.P$4, H1.P$5, H1.P$6, H1.P$7, H1.P$8, H1.P$9, H1.P$10, H1.P$11, H1.P$12, H1.P$13, H1.P$14, H1.P$15, H1.P$16, H1.P$17, H1.P$18, H1.P$19, H1.P$20, H1.P$21, H1.P$22, H1.P$23, H1.P$24, H1.P$25, H1.P$26, H1.P$27, H1.P$28, H1.P$29, H1.P$30, H1.P$31, H1.P$32, IC3.3 (GND), IC3.EXP (GND), IC3.M (GND), J1.GND, J1.GND2 (GND), JP1.3, JP2.1, JP3.1, JP4.1, JP5.1, JP6.3, L2.C, L3.C, L5.C, L9.C, LED2.C, R36.1, R37.1, S1.1, S2.1, S4.4 (R1), S5.4 (R1), S7.4 (R1), S9.4 (R1), T3.2 (E), T4.2 (E), T5.2 (E), T6.2 (E); also elsewhere on the board
IO0: R11.2, S1.3 (2), T1.C; also elsewhere on the board
IO4: JP5.3; also elsewhere on the board
IO5: JP4.3; also elsewhere on the board
IO14: JP3.3; also elsewhere on the board
IO15: JP2.3; also elsewhere on the board
IO16: R3.2, R12.2; also elsewhere on the board
IO17: R6.2, R7.2; also elsewhere on the board
IO18: R10.2, R13.2; also elsewhere on the board
IO19: R16.2, R17.2; also elsewhere on the board
IO23: JP5.2; also elsewhere on the board
IO25: JP4.2; also elsewhere on the board
IO26: JP3.2; also elsewhere on the board
IO27: JP2.2; also elsewhere on the board
unnamed: RL1.SWCOMMON, S4.2 (LC)
unnamed: C2.2, S4.5 (RC), X7.2
unnamed: C2.1, RL1.SWCLOSED (SWCLOSE), X7.1
unnamed: IC3.9 (!RST), R8.2
unnamed: D2.A, RL1.COIL0, T3.3 (C)
unnamed: R3.1, T3.1 (B)
unnamed: D3.A, RL3.COIL0, T4.3 (C)
unnamed: R6.1, T4.1 (B)
unnamed: L3.A, R7.1
unnamed: RL3.SWCOMMON, S5.2 (LC)
unnamed: C6.2, S5.5 (RC), X2.2
unnamed: C6.1, RL3.SWCLOSED (SWCLOSE), X2.1
unnamed: R30.2, T2.B
unnamed: R31.2, T1.B
unnamed: L2.A, R12.1
unnamed: D5.A, RL5.COIL0, T5.3 (C)
unnamed: R10.1, T5.1 (B)
unnamed: L5.A, R13.1
unnamed: RL5.SWCOMMON, S7.2 (LC)
unnamed: C13.2, S7.5 (RC), X4.2
unnamed: C13.1, RL5.SWCLOSED (SWCLOSE), X4.1
unnamed: LED2.A, R22.1
unnamed: D10.A, RL7.COIL0, T6.3 (C)
unnamed: R16.1, T6.1 (B)
unnamed: L9.A, R17.1
unnamed: RL7.SWCOMMON, S9.2 (LC)
unnamed: C15.2, S9.5 (RC), X6.2
unnamed: C15.1, RL7.SWCLOSED (SWCLOSE), X6.1
RTS: IC3.24 (RTS), R31.1, T2.E
RX: IC3.26 (TXD), JP1.1; also elsewhere on the board
SCL: JP6.2; also elsewhere on the board
SDA: JP6.1; also elsewhere on the board
TX: IC3.25 (RXD), JP1.2; also elsewhere on the board
VCC: S4.1 (L1), S5.1 (L1), S7.1 (L1), S9.1 (L1); also elsewhere on the board
V_USB: IC3.7 (REGIN), IC3.8 (VBUS), J1.VBUS1 (VBUS), J1.VBUS2 (VBUS)

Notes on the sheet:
Mounting holes
Serial
Reset & Flash
Pushbuttons
Relays
I2C
CP2102 (USB-to-Serial Converter)
Auto-Reset

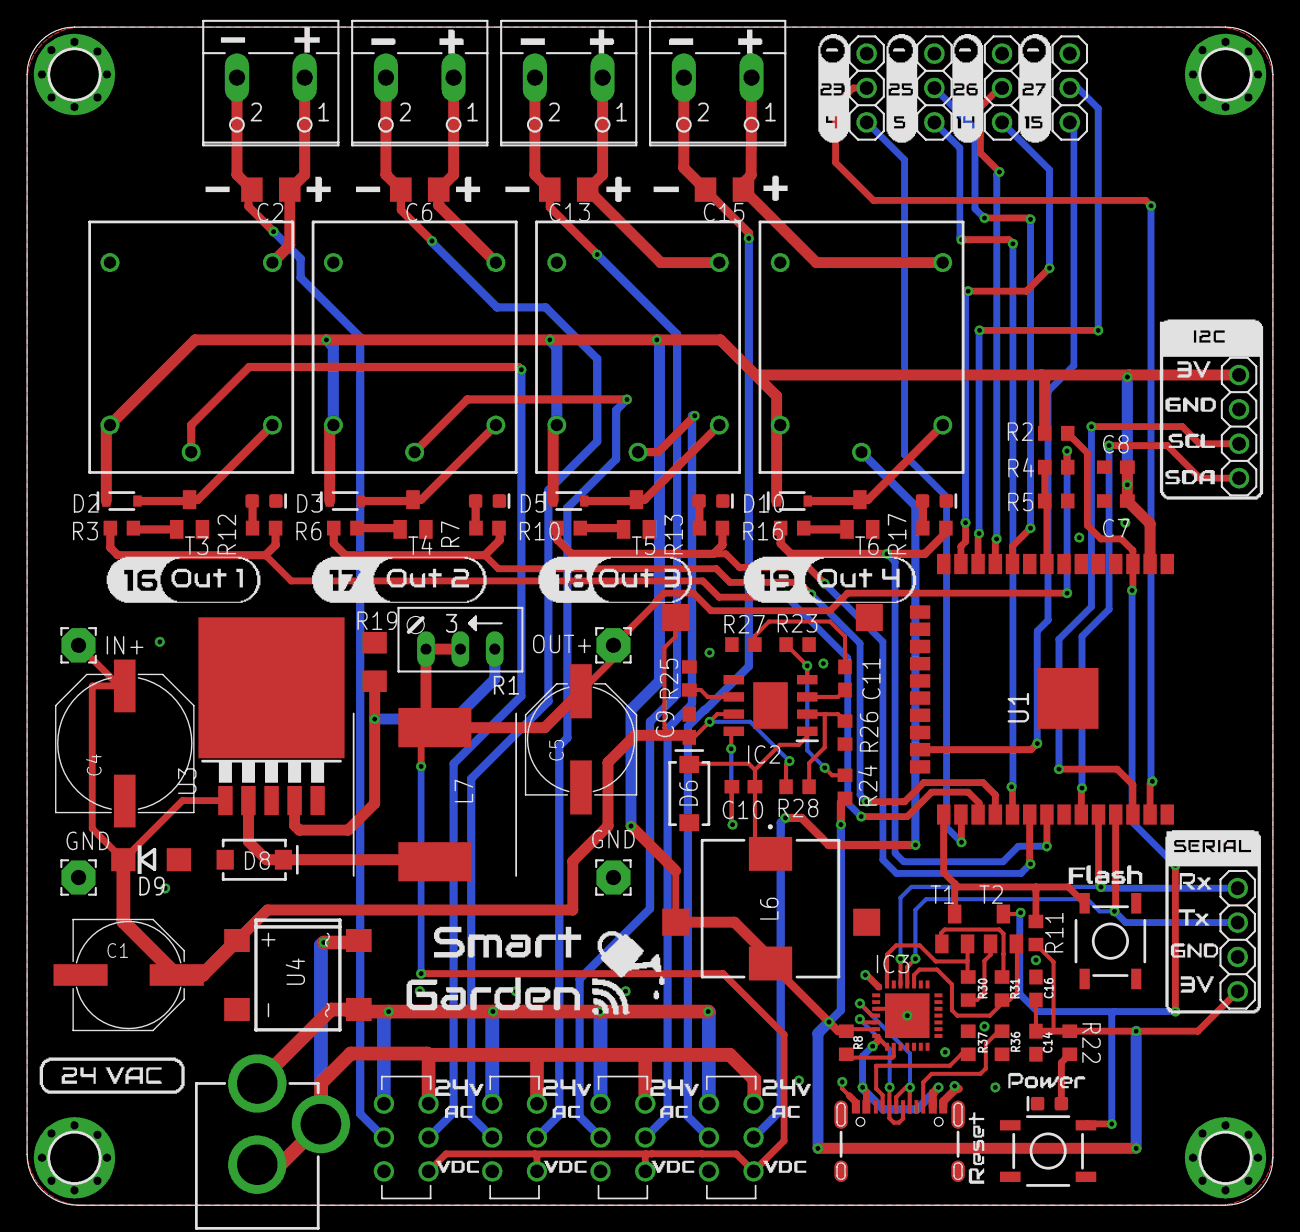
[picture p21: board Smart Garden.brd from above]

Board: 2 copper layers, 92.0 x 87.0 mm, 96 parts (0 on the bottom side), 69 nets.

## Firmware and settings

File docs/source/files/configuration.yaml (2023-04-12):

substitutions:
  device_name: "smart-garden"
  friendly_name: "Smart Garden"
  project_name: "smart.garden"
  project_version: "1.0"
  ap_ssid: "Smart-Garden"
  ap_pwd: "smartgarden"

esphome:
  name: "${device_name}"
  name_add_mac_suffix: true
  project:
    name: "${project_name}"
    version: "${project_version}"

esp32:
  board: esp32dev
  framework:
    type: arduino

# Enable logging
logger:

# Enable Home Assistant API
api:

# Enable Over The Air updates
ota:

#Public location of this yaml file
dashboard_import:
  package_import_url: github://JGAguado/Smart_Garden/docs/source/files/configuration.yaml
  import_full_config: false

# Enable fallback hotspot (captive portal) in case wifi connection fails
captive_portal:

esp32_improv:
  authorizer: none

improv_serial:

wifi:
  ap:
    ssid: "${ap_ssid}"
    password: "${ap_pwd}"

# These relays will automatically turn off after 2 minutes
switch:
  - platform: gpio
    pin: 16
    id: relay_1
    name: "Zone 1"
    icon: "mdi:sprinkler-variant"
    on_turn_on:
    - delay: 120s
    - switch.turn_off: relay_1    
    
  - platform: gpio
    pin: 17
    id: relay_2
    name: "Zone 2"
    icon: "mdi:sprinkler-variant"
    on_turn_on:
      - delay: 120s
      - switch.turn_off: relay_2
    
  - platform: gpio
    pin: 18
    id: relay_3
    name: "Zone 3"
    icon: "mdi:sprinkler-variant"
    on_turn_on:
      - delay: 120s
      - switch.turn_off: relay_3      
    
  - platform: gpio
    pin: 19
    id: relay_4
    name: "Zone 4"
    icon: "mdi:sprinkler-variant"
    on_turn_on:
      - delay: 120s
      - switch.turn_off: relay_4  

sensor:
  - platform: adc
    pin: A4
    name: "VCC"
    update_interval: 60s
    filters:
      - calibrate_linear:
          - 0 -> 0
          - 0.55 -> 5

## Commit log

2022-04-13 Added silkscreen designs
2022-04-13 Added design files
    [Smart Garden.brd, Smart Garden.sch]
2022-04-24 Removed dimension drawings from brd and reloaded images
    [Smart Garden.brd]
2022-08-09 First commit to the CP2102 branch with schematic and a first layout of the CP2102
    [Smart Garden.brd, Smart Garden.sch]
2022-08-20 First commit to the CP2102 branch
    [Smart Garden.brd, Smart Garden.sch]
2022-09-26 Updated design files
    [Smart Garden.brd, Smart Garden.sch]
2022-10-06 Updated Silkscreen
2023-02-23 Silkscreen fixed
    [Smart Garden.brd]

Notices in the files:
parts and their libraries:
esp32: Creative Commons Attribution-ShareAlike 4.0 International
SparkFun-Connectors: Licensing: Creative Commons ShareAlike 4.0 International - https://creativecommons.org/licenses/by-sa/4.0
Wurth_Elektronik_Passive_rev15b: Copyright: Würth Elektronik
